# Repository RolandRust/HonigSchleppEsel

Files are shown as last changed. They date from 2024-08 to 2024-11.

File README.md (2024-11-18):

# HonigSchleppEsel
Turntable addon for the HaniMandl

## Kompiliert nur mit Visual Studio Code. Mit der Arduino IDE gibts Probleme!

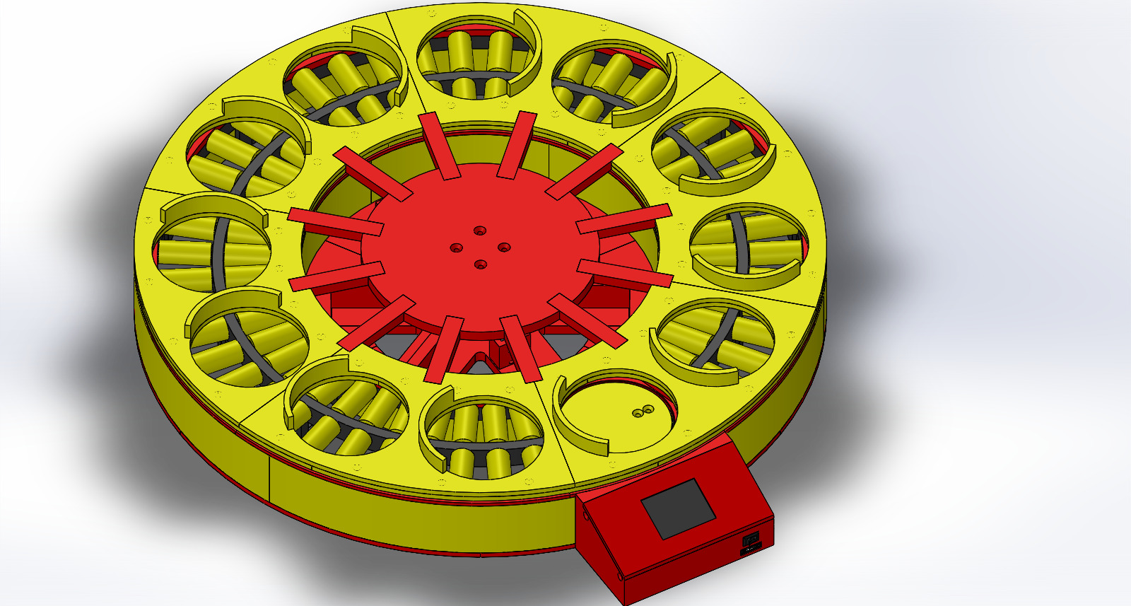
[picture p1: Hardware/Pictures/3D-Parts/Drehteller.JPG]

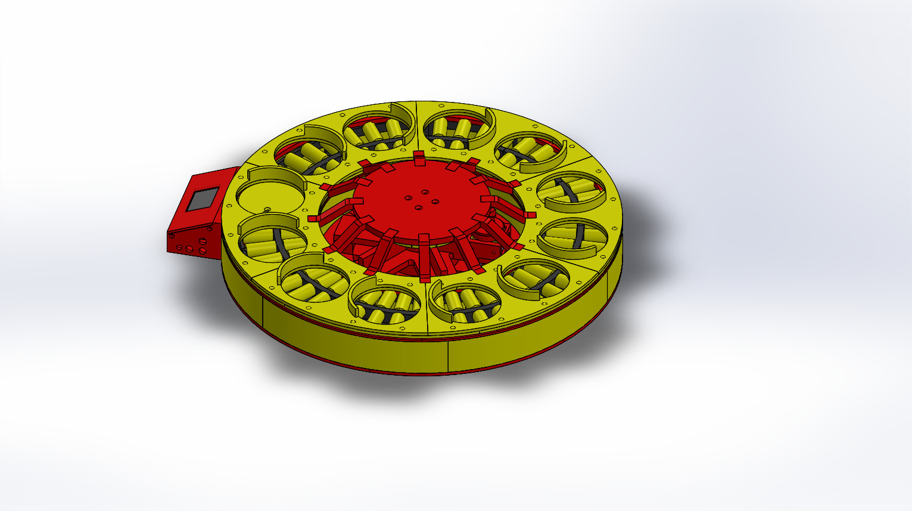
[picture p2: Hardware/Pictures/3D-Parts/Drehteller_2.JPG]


https://www.youtube.com/watch?v=Gq03sCifO4o

dev version

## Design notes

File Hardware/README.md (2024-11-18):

# Hardware
## Bottom middle assembly
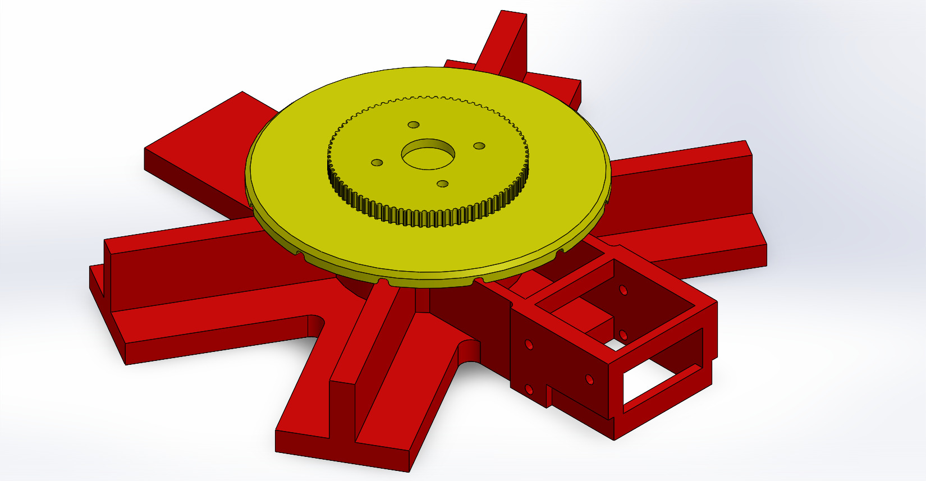
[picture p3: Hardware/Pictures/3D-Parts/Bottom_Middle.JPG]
bottom_middle

## Bottom middle optical switch assembly
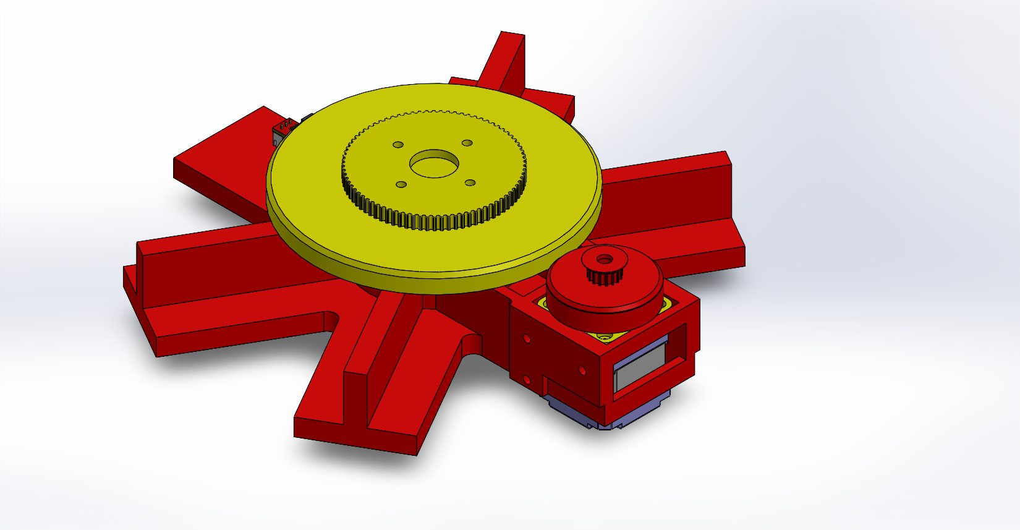
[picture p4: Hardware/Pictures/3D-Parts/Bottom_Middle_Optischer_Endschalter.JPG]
bottom_middle_optischer_endschalter

### Bottom_Middle
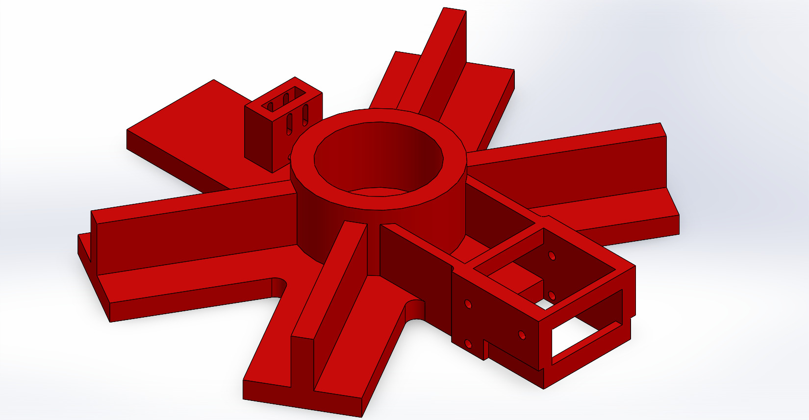
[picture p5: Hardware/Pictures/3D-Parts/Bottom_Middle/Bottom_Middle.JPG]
bottom_middle

### Bottom_Middle_Optischer_Schalter
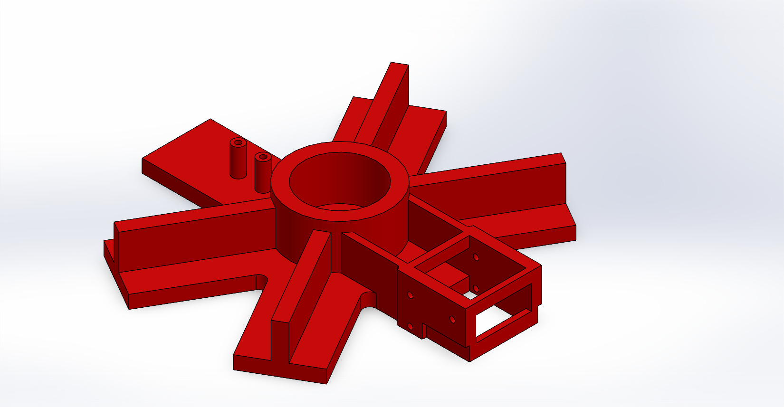
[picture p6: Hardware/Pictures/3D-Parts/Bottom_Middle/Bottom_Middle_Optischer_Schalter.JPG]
bottom_middle_optischer_schalter

### Mittelteil_Addon_30mm
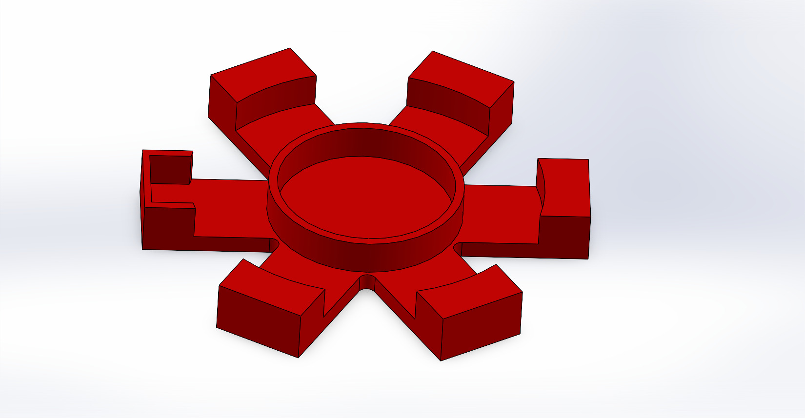
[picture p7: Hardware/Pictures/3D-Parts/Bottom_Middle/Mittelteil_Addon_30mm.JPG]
mittelteil_addon_30mm

### Umbau_zu_Optischem_Switch_Teil_1
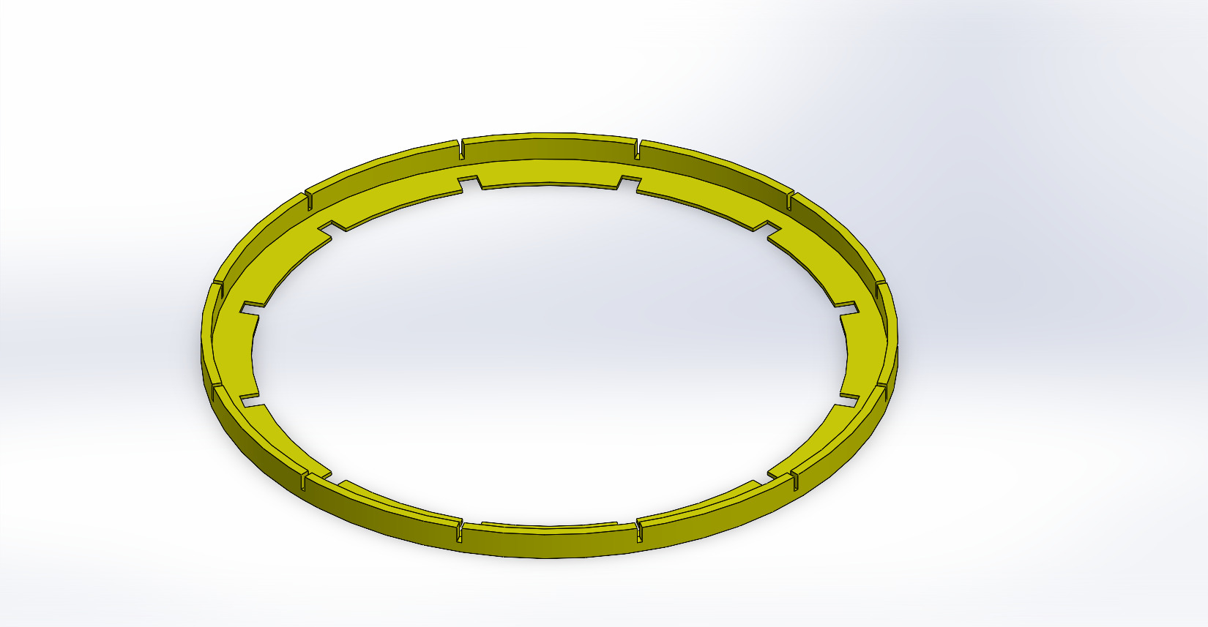
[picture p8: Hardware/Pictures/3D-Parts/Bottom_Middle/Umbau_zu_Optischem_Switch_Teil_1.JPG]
umbau_zu_optischem_switch_teil_1

### Umbau_zu_Optischem_Switch_Teil_2
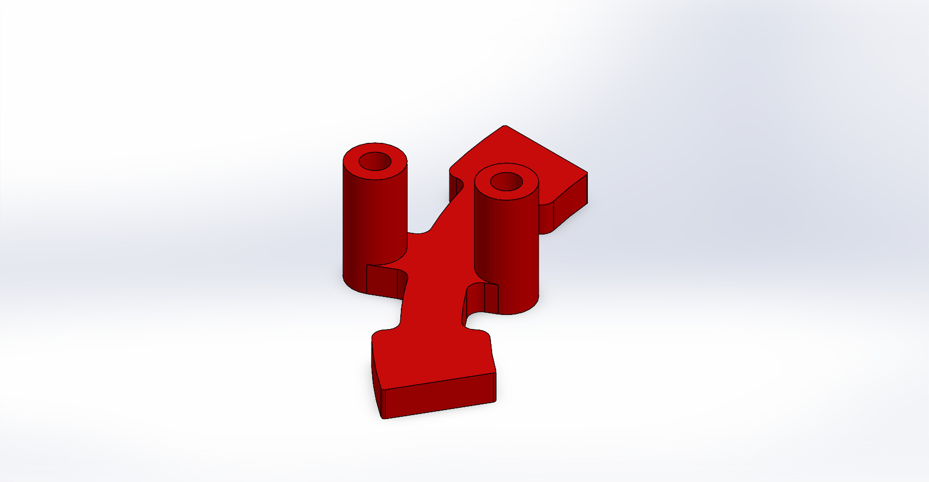
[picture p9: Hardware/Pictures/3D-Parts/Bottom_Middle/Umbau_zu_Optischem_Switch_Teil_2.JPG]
umbau_zu_optischem_switch_teil_2

### Umbau_zu_Optischem_Switch_Teil_3
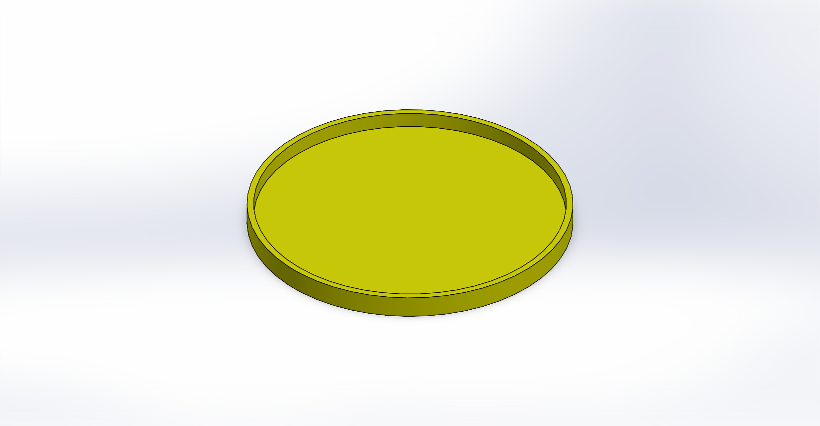
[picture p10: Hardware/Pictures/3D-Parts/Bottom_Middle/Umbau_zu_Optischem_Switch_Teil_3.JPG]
umbau_zu_optischem_switch_teil_3

### Mittelteil_Drehelement
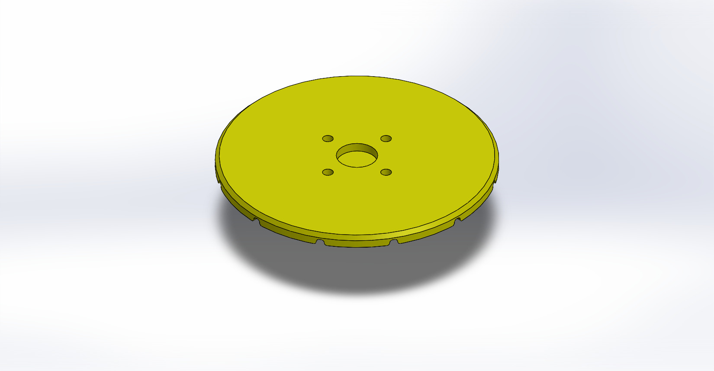
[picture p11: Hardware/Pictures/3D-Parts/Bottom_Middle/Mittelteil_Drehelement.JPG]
bottom_middle

### Mittelteil_Drehelement_Optischer_Endschalter
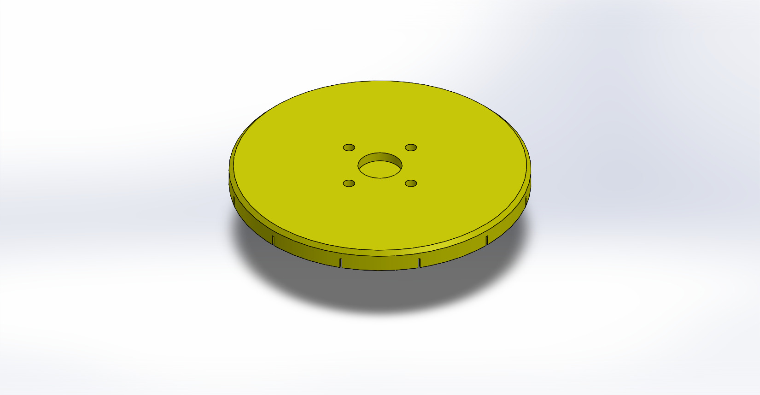
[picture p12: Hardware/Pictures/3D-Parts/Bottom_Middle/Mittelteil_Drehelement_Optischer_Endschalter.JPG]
bottom_middle

### HTD3_80_6.5
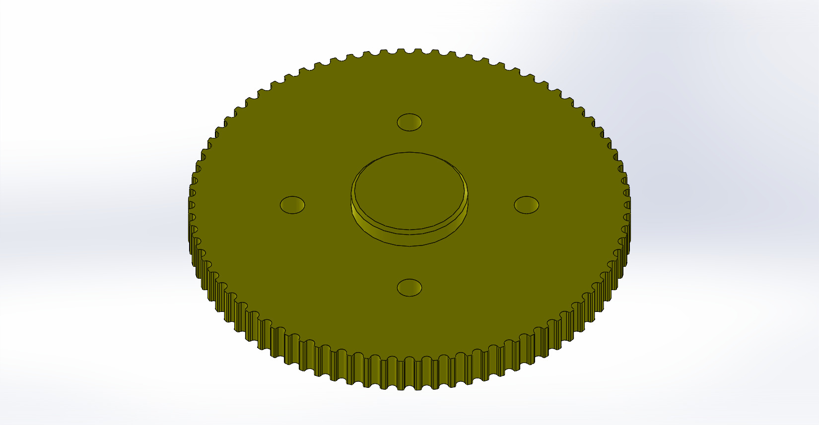
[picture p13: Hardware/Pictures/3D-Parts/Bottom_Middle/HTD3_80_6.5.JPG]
bottom_middle


## Bottom assembly
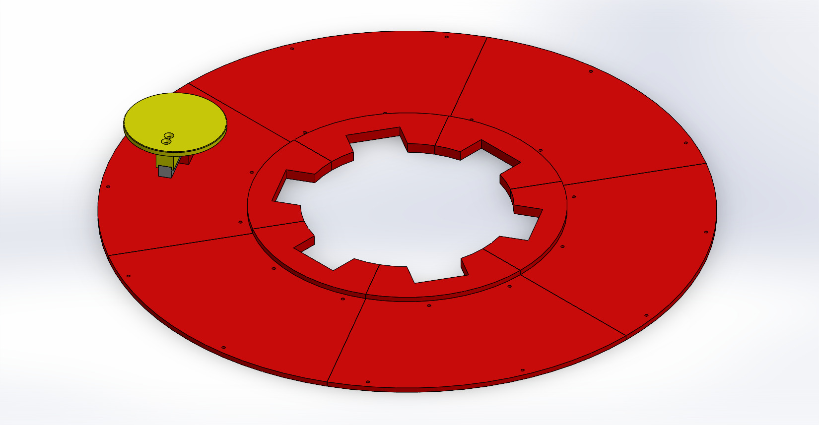
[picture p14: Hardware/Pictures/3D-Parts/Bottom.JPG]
bottom

### Bottom_Out
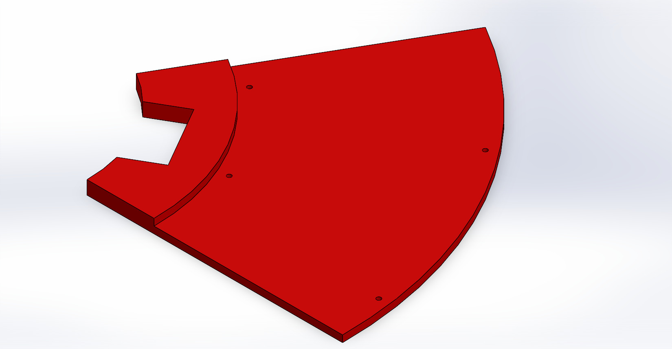
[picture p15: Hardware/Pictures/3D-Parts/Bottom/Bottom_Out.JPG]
bottom

### Bottom_Out_Scale
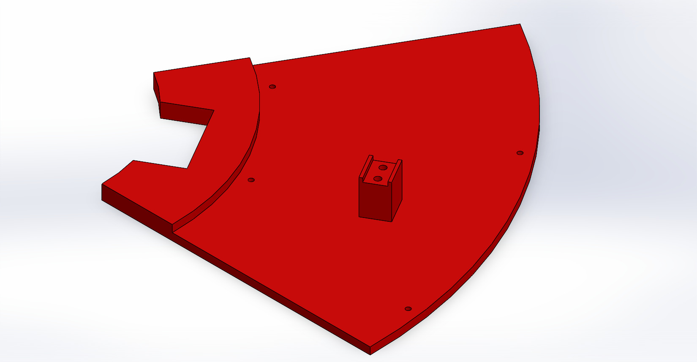
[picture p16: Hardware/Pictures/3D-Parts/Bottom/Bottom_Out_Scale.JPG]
bottom

### Scale_Top
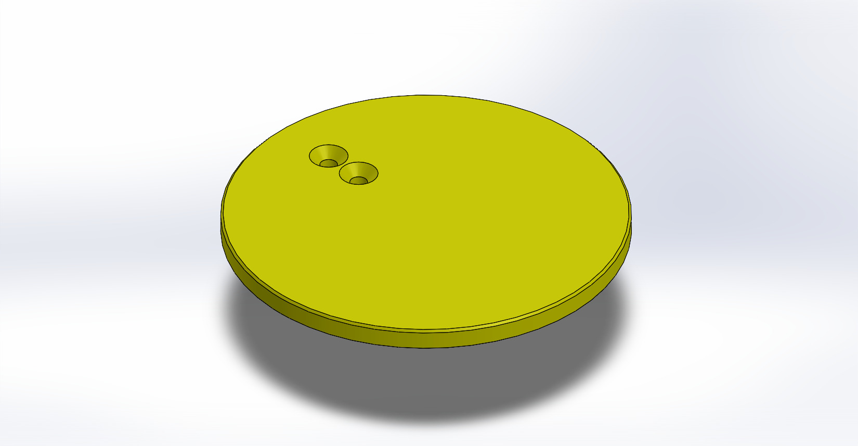
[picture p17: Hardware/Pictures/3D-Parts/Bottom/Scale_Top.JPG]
bottom


## 	Roll holder assembly
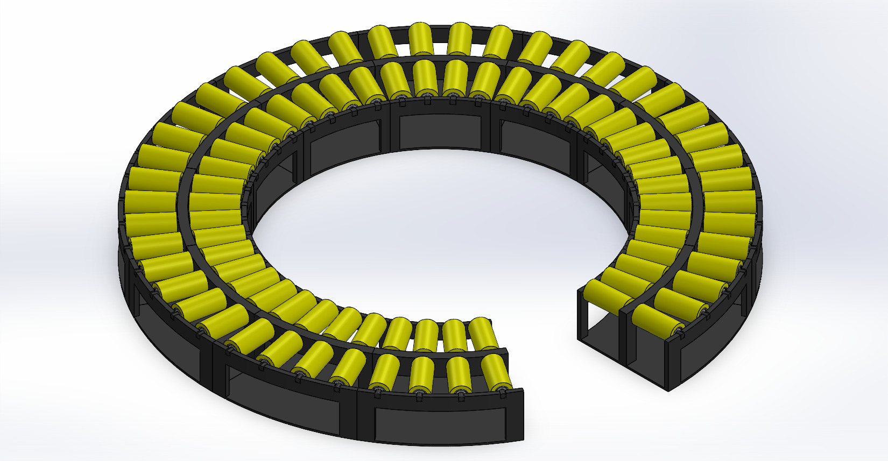
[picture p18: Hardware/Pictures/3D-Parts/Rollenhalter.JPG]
roll_holder

### Rollenhalter_klein
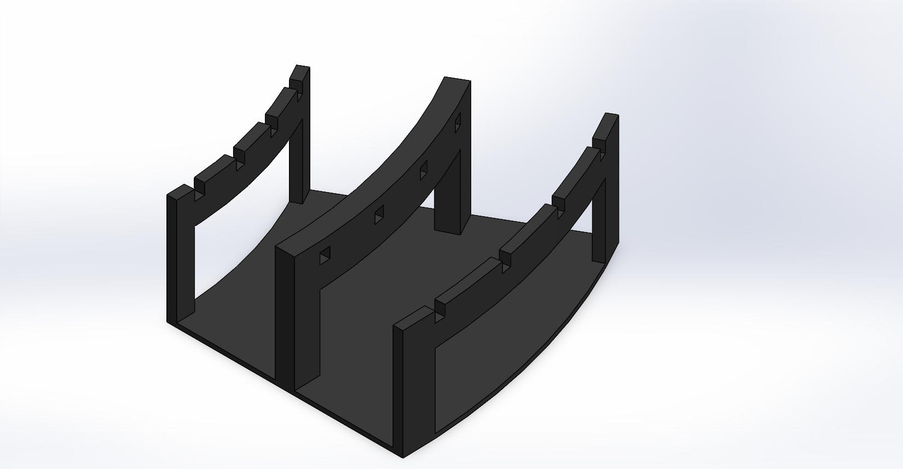
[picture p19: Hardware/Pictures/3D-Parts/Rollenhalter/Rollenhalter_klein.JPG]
roll_holder

### Rolle
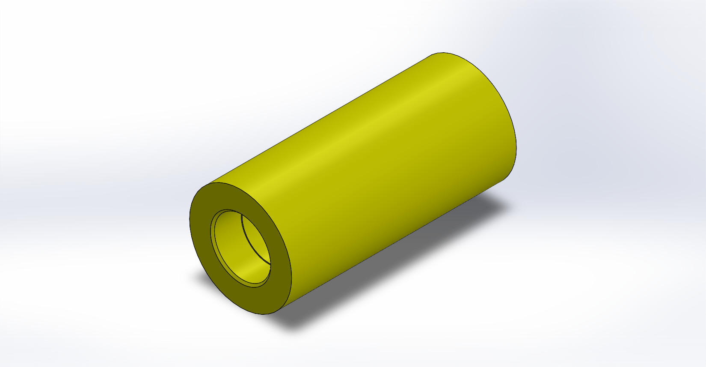
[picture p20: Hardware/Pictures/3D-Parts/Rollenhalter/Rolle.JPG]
roll_holder

### Zylinder_Stift
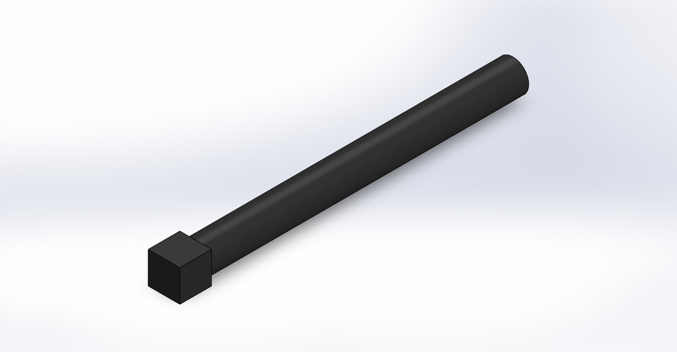
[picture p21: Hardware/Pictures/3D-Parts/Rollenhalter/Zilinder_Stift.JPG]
roll_holder


## 	Bottom top assembly
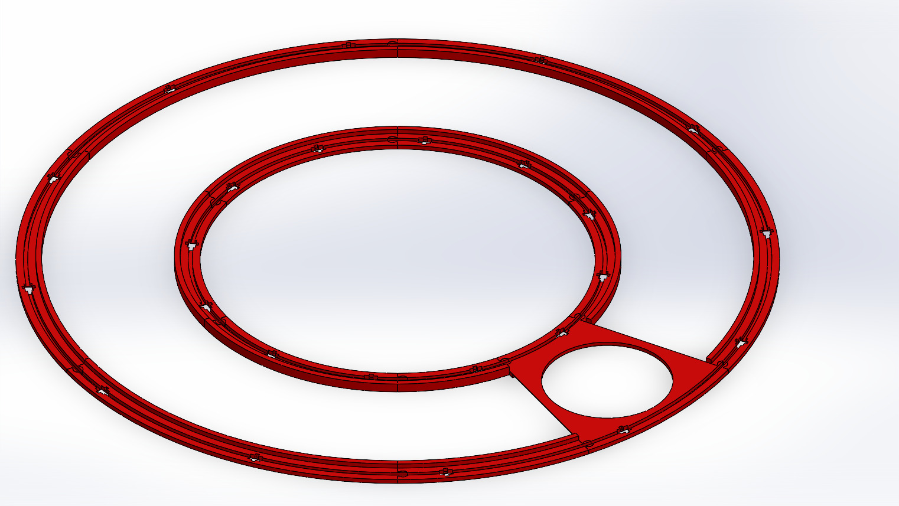
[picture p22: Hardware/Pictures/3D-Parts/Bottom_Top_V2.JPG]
bottom_top

### Top_Scale_V2
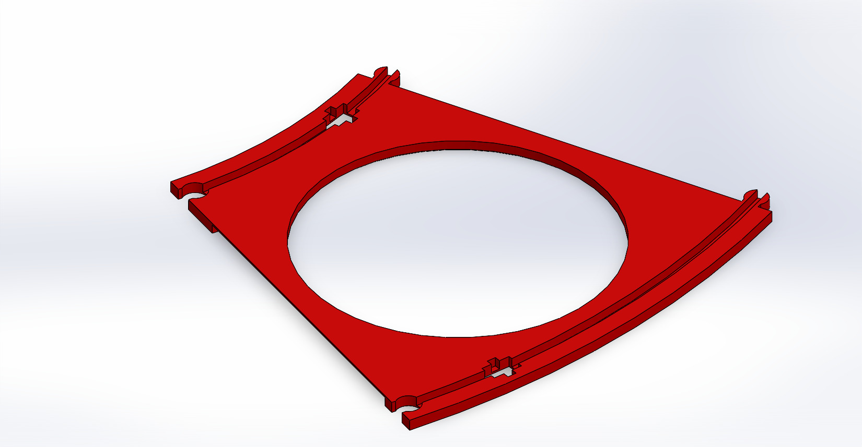
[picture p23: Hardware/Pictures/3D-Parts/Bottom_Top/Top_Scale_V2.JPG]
bottom_top

### Top_Ring_Big_Inside_V2
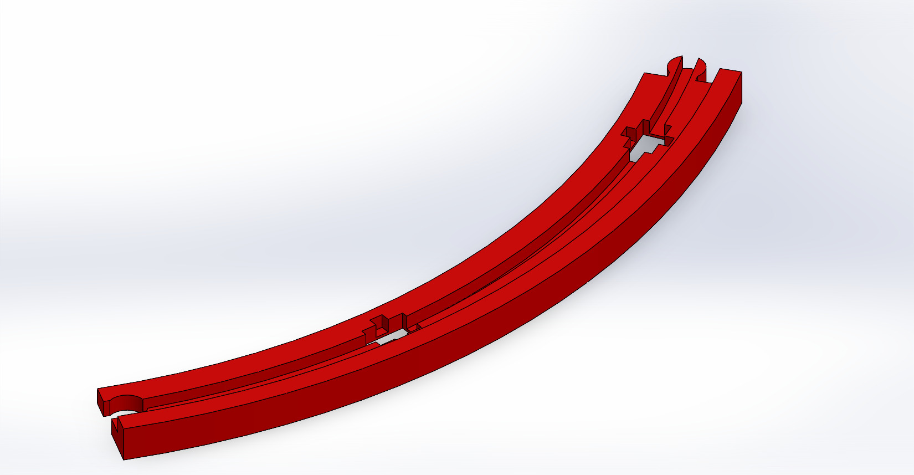
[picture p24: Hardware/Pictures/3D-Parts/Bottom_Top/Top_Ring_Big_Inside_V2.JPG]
bottom_top

### Top_Ring_Big_Outer_V2
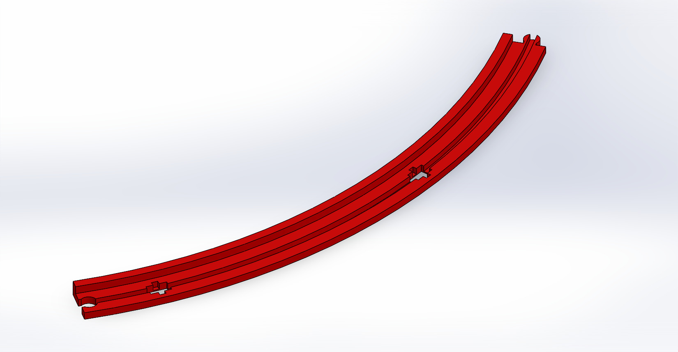
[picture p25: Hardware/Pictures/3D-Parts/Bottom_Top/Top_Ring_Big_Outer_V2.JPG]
bottom_top

### Top_Ring_Small_Inside_V2
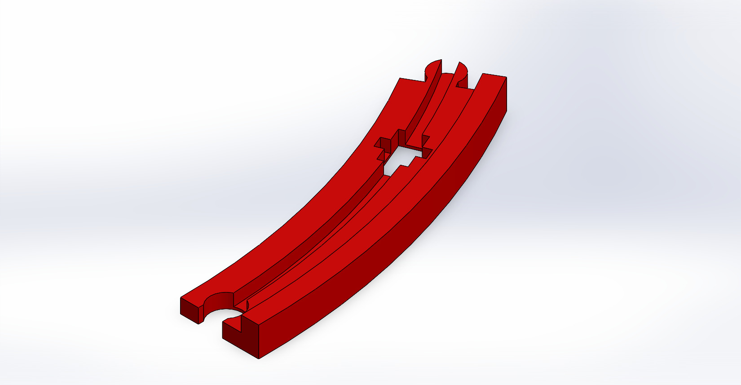
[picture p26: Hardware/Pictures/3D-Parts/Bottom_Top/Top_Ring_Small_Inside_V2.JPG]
bottom_top

### Top_Ring_Small_Outer_V2
bottom_top

## 	Wall inside assembly
wall_inside
### Wall_Inside_V2
wall_inside

## 	Wall outside assembly
wall_outside
### Wall_Inside_V2
wall_outside

## 	Top assembly
top
## 	Top_30mm assembly
top_30mm
### Top_Mittelteil_Drehelement
top
### Top_Jar_Mover_1
top
### Top_Jar_Mover_2
top
### Top_Holm
top
### Top_Holm_30mm
top_holm_30mm

## 	Front box
front_box
### Box_Bottom
front_box
### Box_Top
front_box

## 	Gear box
gear_box
### Carrier_Plate
gear_box
### Ring
gear_box
### Gear_Planet_0.5
gear_box
###Gear_Stepper_0.5
gear_box

## Fixes
### FIX_1
fixes
### FIX_2
fixes

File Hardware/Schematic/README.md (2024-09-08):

# Schematic
schematic

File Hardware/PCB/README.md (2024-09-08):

# PCB
PCB
PCB

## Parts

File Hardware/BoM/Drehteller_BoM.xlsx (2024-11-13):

Drehteller Stückliste (flache Version mit mechanischem Endschalter --> Motor schaut unter raus)
Version 1: | Flach mit mechanischem Taster für die Glaspositionierung (Stepper schaut unten raus)
Version 2: | Flach mit optischem Schalter für die Glaspositionierung (Stepper schaut unten raus)
Version 3: | Umbau der Version 1 auf optischen Schalter für die Glaspositionierung (Stepper schaut unten raus)
Version 4: | Umbau der Version 1 auf optischen Schalter für die Glaspositionierung und Erhöhung von dem Mittelteil (Stepper schaut unten nicht raus)
Version 5: | Optischer Endschalter für die Glaspositionierung und Erhöhung vom Mittelteil --> empfohlene Version
Remarks: | Wenn mein Pseudo Getriebe aufgiebt, werde ich es durch ein gekaugtes ersetzen. Für ein gekauftes Getriebe muss noch eine Befestigung ausgedacht werden.
 | Version 1 | Version 2 | Version 3 | Version 4 | Version 5
Bottom_Middle
POS | Anzahl | Anzahl | Anzahl | Anzahl | Anzahl | Beschreibung
1 | 1 | - | 1 | 1 | - | Bottom_Middle | 3D Druck
2 | - | 1 | - | - | 1 | Bottom_Middle_Optischer_Schalter | 3D Druck
3 | - | - | - | 1 | 1 | Mittelteil_Addon_30mm | 3D Druck
4 | - | - | - | - | - | Bottom_Middle_30mm (noch nicht gezeichnet) | 3D Druck | ersetzt Bottom_Middle_Optischer_Schalter und Mittelteil_Addon_30mm vei der Variante 5
5 | 1 | - | 1 | 1 | - | Mittelteil_Drehelement | 3D Druck
6 | - | 1 | - | - | 1 | Mittelteil_Drehelement_Optischer_Endschalter (noch nicht gezeichnet) | 3D Druck | noch nicht fertig gezeichnet
7 | 1 | 1 | 1 | 1 | 1 | HTD3_80_6.5 | 3D Druck
8 | - | - | - | 1 | - | Umbau_zu_Optischem_Switch_Teil_1 | 3D Druck | mit schwarzem PET drucken. Durch gelbes PETG konnte bei mir der optische Schalter durchsehen.
9 | - | - | - | 1 | - | Umbau_zu_Optischem_Switch_Teil_2 | 3D Druck
10 | - | - | - | 1 | - | Umbau_zu_Optischem_Switch_Teil_3 | 3D Druck
11 | 1 | - | 1 | - | - | Mikro Schalter Endschalter mit Momentanem Roller Hebel Arm SPDT | gekauft
12 | - | 1 | - | 1 | 1 | TCST2103 Optische Endstop Light Control Begrenzung Optische Schalter für 3D Drucker | gekauft
13 | 1 | 1 | 1 | 1 | 1 | Axial-Nadelkranz AXK3047 mit 2 Unterlagssccheiben | gekauft
14 | 1 | 1 | 1 | 1 | 1 | Nadellager Radial 50*55*27mm K505527 | gekauft
15 | 2 | 2 | 2 | 2 | 2 | Schraube, Mutter und Unterlagsscheibe für Mikro Endschalter | gekauft
16 | 4 | 4 | 4 | 4 | 4 | Gewindeeinsätze für 3D Druck M4xL8xOD6 | gekauft
17 | 1 | 1 | 1 | 1 | 1 | HTD 3M Zahnriemen 6mm x 351mm | gekauft
Top
POS | Anzahl | Anzahl | Anzahl | Anzahl | Anzahl | Beschreibung
1 | 6 | 6 | 6 | 6 | 6 | Top_Jar_Mover_1 | 3D Druck
2 | 6 | 6 | 6 | 6 | 6 | Top_Jar_Mover_2 | 3D Druck
3 | 12 | 12 | 12 | - | - | Top_Holm | 3D Druck
4 | - | - | - | 12 | 12 | Top_Holm_30mm | 3D Druck
5 | 1 | 1 | 1 | 1 | 1 | Top_Mittelteil_Drehelement | 3D Druck
5 | 4 | 4 | 4 | 4 | 4 | Schrauben | gekauft
Rollenhalter
POS | Anzahl | Anzahl | Anzahl | Anzahl | Anzahl | Beschreibung
1 | 11 | 11 | 11 | 11 | 11 | Rollenhalter_klein | 3D Druck
2 | 88 | 88 | 88 | 88 | 88 | Rolle | 3D Druck
3 | 88 | 88 | 88 | 88 | 88 | Zilinder_Stift | 3D Druck
4 | 176 | 176 | 176 | 176 | 176 | Rillenkugellager 685zz | gekauft
Bottom_Top
POS | Anzahl | Anzahl | Anzahl | Anzahl | Anzahl | Beschreibung
1 | 1 | 1 | 1 | 1 | 1 | Top_Scale_V2 | 3D Druck
2 | 5 | 5 | 5 | 5 | 5 | Top_Ring_Big_Inside_V2 | 3D Druck
3 | 1 | 1 | 1 | 1 | 1 | Top_Ring_Smal_Inside_V2 | 3D Druck
4 | 5 | 5 | 5 | 5 | 5 | Top_Ring_Big_Outer_V2 | 3D Druck
5 | 1 | 1 | 1 | 1 | 1 | Top_Ring_Small_Inside_V2 | 3D Druck
Wall_Inside
POS | Anzahl | Anzahl | Anzahl | Anzahl | Anzahl | Beschreibung
1 | 6 | 6 | 6 | 6 | 6 | Wall_Inside_V2 | 3D Druck
2 | 12 | 12 | 12 | 12 | 12 | Rillenkugellager 693zz | gekauft
3 | 12 | 12 | 12 | 12 | 12 | Zylinderstift M3x10mm | gekauft
4 | 12 | 12 | 12 | 12 | 12 | Gewindeeinsätze für 3D Druck M3xL8xOD5 | gekauft
5 | 12 | 12 | 12 | 12 | 12 | Schrauben zur Besestigung an die Baugruppe Bottom | gekauft
Wall_Outside
POS | Anzahl | Anzahl | Anzahl | Anzahl | Anzahl | Beschreibung
1 | 6 | 6 | 6 | 6 | 6 | Wall_Outside_V2 | 3D Druck
2 | 12 | 12 | 12 | 12 | 12 | Rillenkugellager 693zz | gekauft
3 | 12 | 12 | 12 | 12 | 12 | Zylinderstift M3x10mm | gekauft
4 | 12 | 12 | 12 | 12 | 12 | Gewindeeinsätze für 3D Druck M3xL8xOD5 | gekauft
5 | 12 | 12 | 12 | 12 | 12 | Schrauben zur Besestigung an die Baugruppe Bottom | gekauft
Bottom
POS | Anzahl | Anzahl | Anzahl | Anzahl | Anzahl | Beschreibung
1 | 1 | 1 | 1 | 1 | 1 | Bottom_Out_Scale | 3D Druck
2 | 5 | 5 | 5 | 5 | 5 | Bottom_Out | 3D Druck
3 | 1 | 1 | 1 | 1 | 1 | Scale_Top | 3D Druck
4 | 1 | 1 | 1 | 1 | 1 | Wägezelle 5kg | gekauft
5 | 4 | 4 | 4 | 4 | 4 | Schrauben für die Waage | gekauft
Front
POS | Anzahl | Anzahl | Anzahl | Anzahl | Anzahl | Beschreibung
1 | 1 | 1 | 1 | 1 | 1 | Box_Bottom | 3D Druck
2 | 1 | 1 | 1 | 1 | 1 | Box_Top | 3D Druck
3 | 4 | 4 | 4 | 4 | 4 | Gewindeeinsätze für 3D Druck M3xL8xOD5 | gekauft
4 | 4 | 4 | 4 | 4 | 4 | Schrauben zur befestigung des Deckels | gekauft
Pseudo Planeten Getriebe
POS | Anzahl | Anzahl | Anzahl | Anzahl | Anzahl | Beschreibung
1 | 1 | 1 | 1 | 1 | 1 | Carrier_Plate | 3D Druck
2 | 1 | 1 | 1 | 1 | 1 | Ring | 3D Druck
3 | 4 | 4 | 4 | 4 | 4 | Gear_Planet_0.5 | 3D Druck
4 | 1 | 1 | 1 | 1 | 1 | Gear_Stepper_0.5 | 3D Druck
5 | 4 | 4 | 4 | 4 | 4 | Schrauben zur Besestigung der Gearbox am Stepper | gekauft
6 | 1 | 1 | 1 | 1 | 1 | NEMA17 Stepper Motor h: 40mm | gekauft
7 | 4 | 4 | 4 | 4 | 4 | Schrauben zur Besestigung von dem NEMA17 an der Baugruppe Bottom_Middle | gekauft
Fixes (ja die braucht es :-))
POS | Anzahl | Anzahl | Anzahl | Anzahl | Anzahl | Beschreibung
1 | 3 | 3 | 3 | 3 | 3 | FIX_1 | 3D Druck
2 | 1 | 1 | 1 | 1 | 1 | FIX_2 | 3D Druck
Diverser
POS | Anzahl | Anzahl | Anzahl | Anzahl | Anzahl | Beschreibung
1 | 1 | 1 | 1 | 1 | 1 | Leim nach Wahl | gekauft

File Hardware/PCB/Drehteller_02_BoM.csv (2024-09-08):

# | Quantity | RefDes | Manufacturer | Order Number | Description
1 | 1 | C1 | RND components | RND 150VVT050M101FB3 | Miniature Aluminium Electrolytic Capacitor 100uF 50V ±20% 8x10.5mm
2 | 1 | D1 | Nexperia | PMEG4030EP | 40 V, 3 A low VF Schottky barrier rectifier
3 | 5 | J1, J3, J5, J11, J12 | Diverse | - | JST XH 2pol Connector 2.54mm (not orginal JST standart)
4 | 7 | J2, J6, J7, J8, J9, J15, J17 | Diverse | - | JST XH 4pol Connector 2.54mm (not orginal JST standart)
5 | 3 | J4, J18, J19 | Diverse | - | JST XH 3pol Connector 2.54mm (not orginal JST standart)
6 | 1 | J10 | Samtec | TSW-104-07-G-S | 1x4 Pol Connector 100mil
7 | 1 | J16 | Diverse | - | JST XH 7pol Connector 2.54mm (not orginal JST standart)
8 | 1 | M1 | Diverse | - | ESP32 NodeMCU Module WLAN WiFi Development Board Socket
9 | 1 | M2 | Diverse | - | MP1584 Module Socket
10 | 1 | M3 | Diverse | - | TMC2209 Silent Stepper Stick Socket
11 | 4 | R1, R2, R3, R4 | Vishay | MCT06030Z0000ZP500 | Resistor 0R 1% 0603

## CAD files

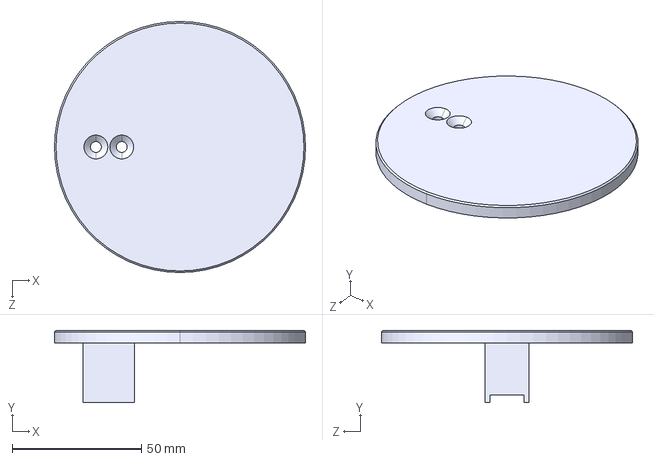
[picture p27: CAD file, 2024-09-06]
Hardware/STEP-Files/Bottom/Scale_Top.STEP
97.0 x 28.0 x 97.0 mm

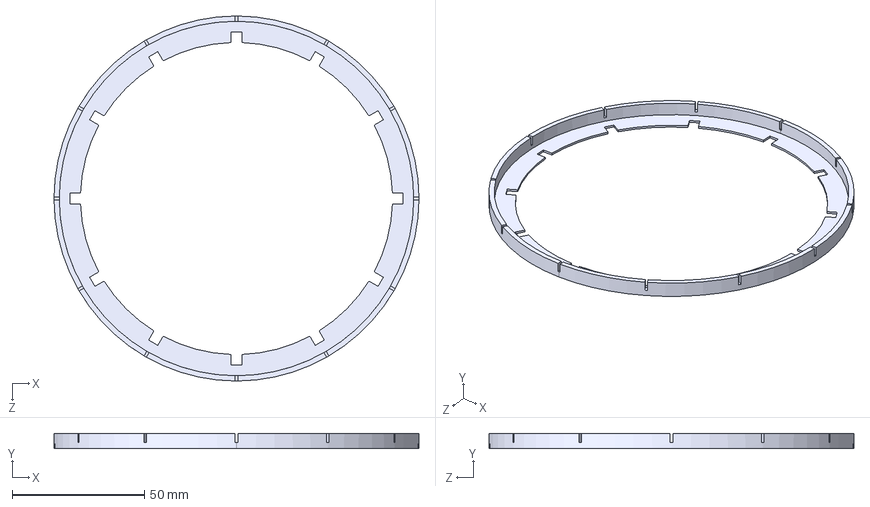
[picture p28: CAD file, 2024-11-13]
Hardware/STEP-Files/Bottom_Middle/Umbau_zu_Optischem_Switch_Teil_1.STEP
138.0 x 5.80 x 138.0 mm

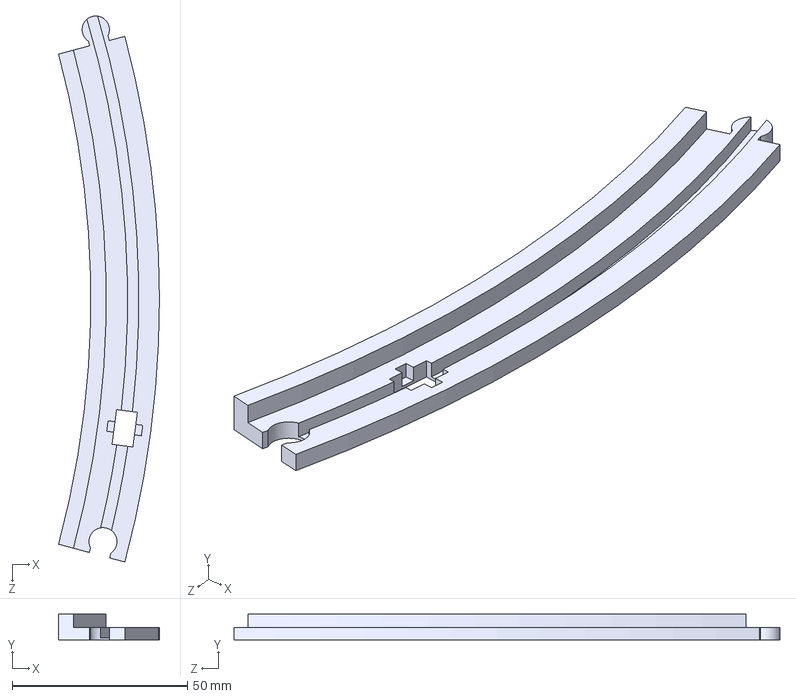
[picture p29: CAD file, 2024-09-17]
Hardware/STEP-Files/Bottom_Top/Top_Ring_Small_Outer_V2.STEP
28.8 x 7.40 x 155.9 mm

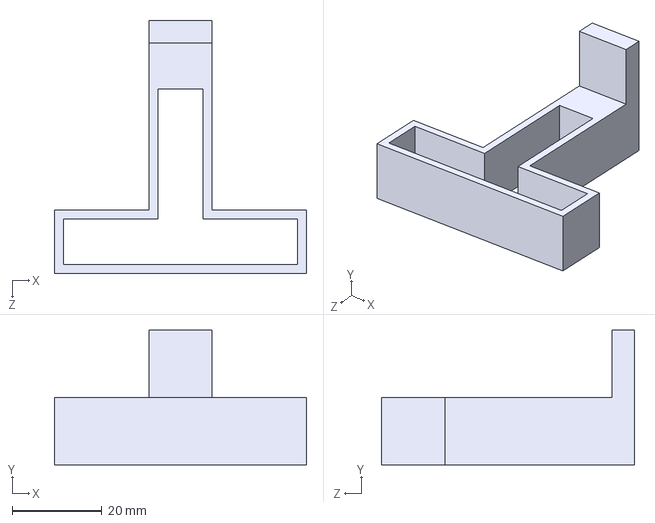
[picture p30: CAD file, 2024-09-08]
Hardware/STEP-Files/Fixes/FIX_1.STEP
56.1 x 30.0 x 56.3 mm

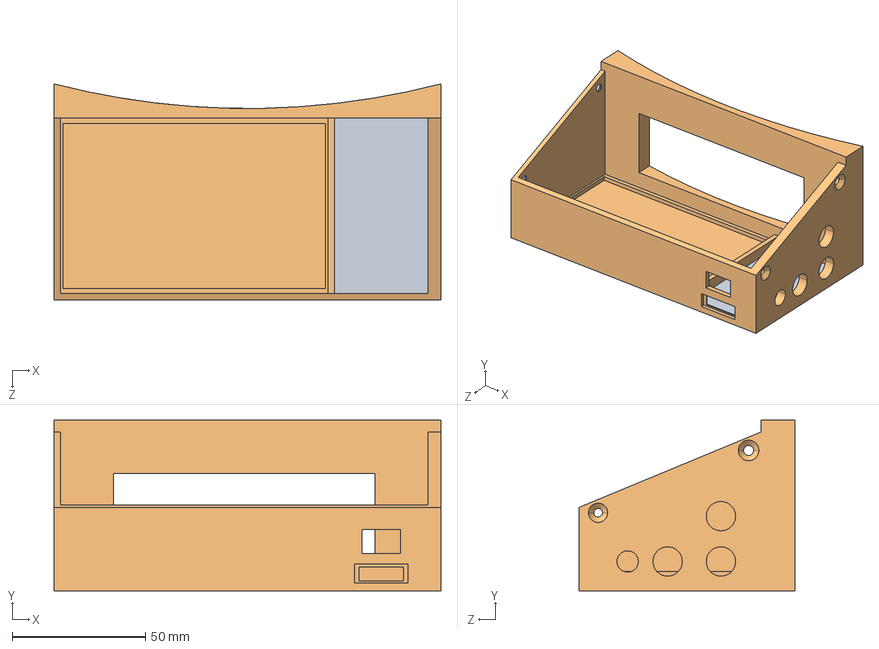
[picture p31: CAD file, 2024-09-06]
Hardware/STEP-Files/Front_Box/Box_Bottom.STEP
145.2 x 64.0 x 81.1 mm

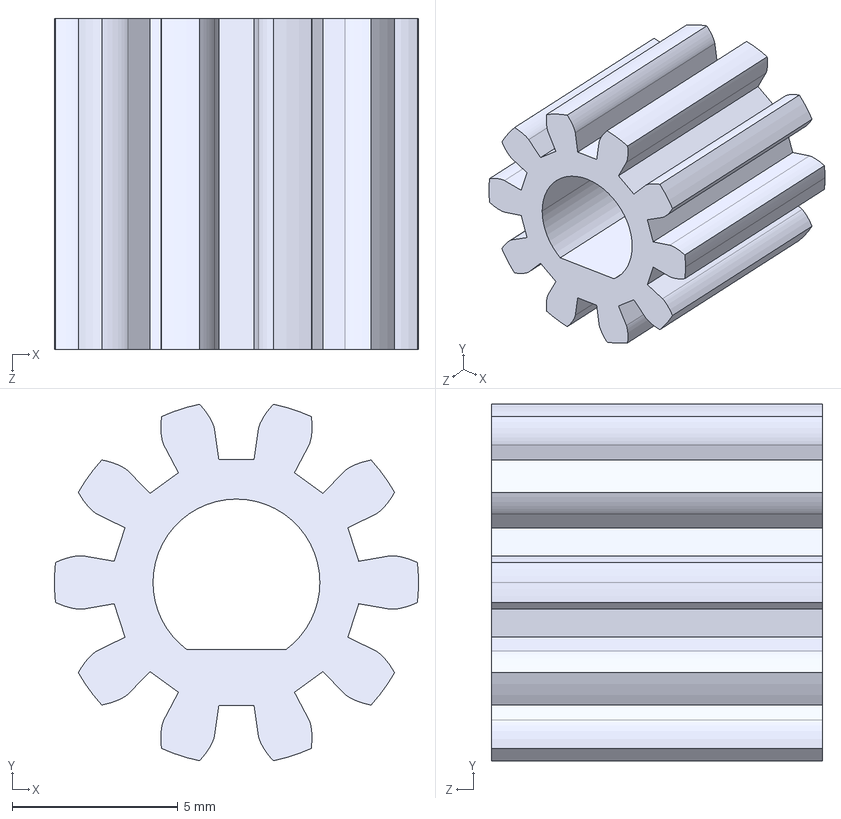
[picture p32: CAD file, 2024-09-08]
Hardware/STEP-Files/GearBox/Gear_Stepper_0.5.STEP
11.0 x 10.8 x 10.0 mm

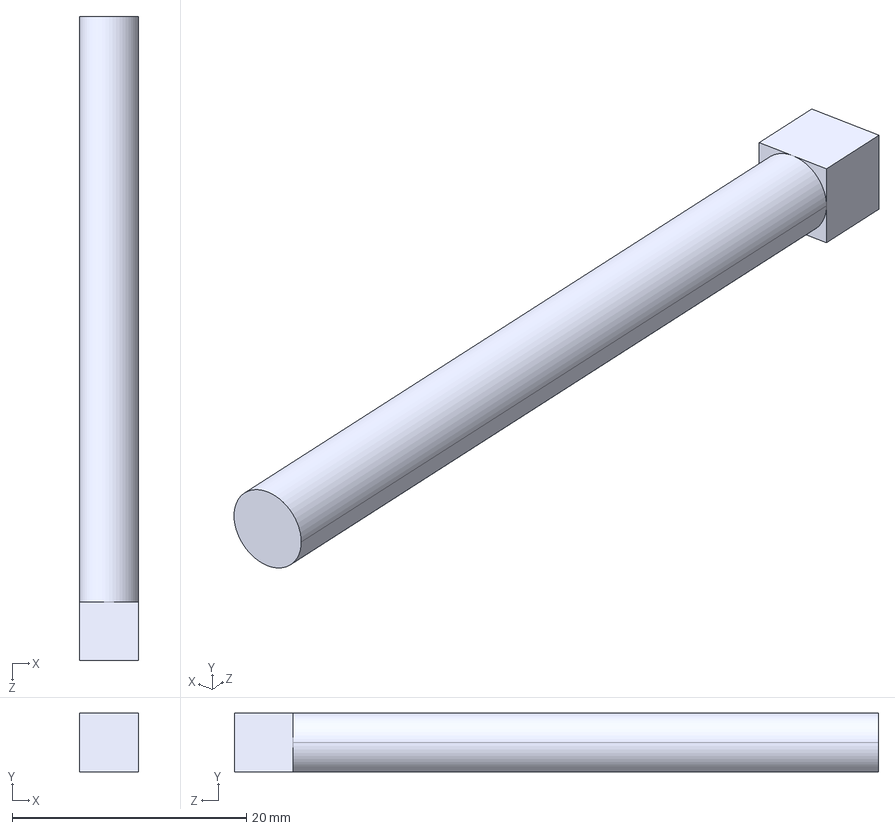
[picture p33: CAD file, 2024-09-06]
Hardware/STEP-Files/Rollenhalter/Zilinder_Stift.STEP
5.00 x 5.00 x 55.0 mm

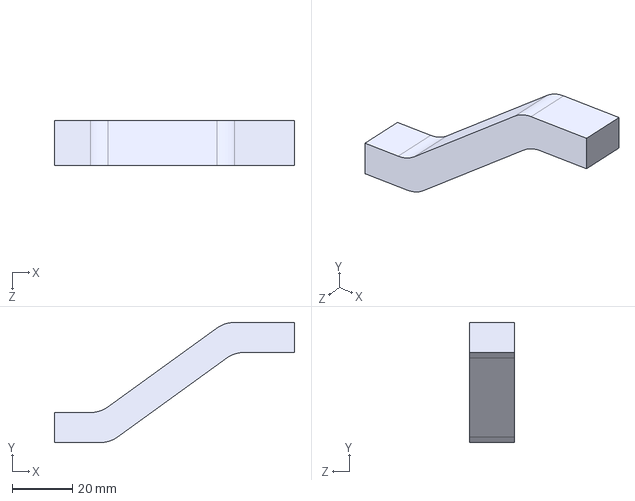
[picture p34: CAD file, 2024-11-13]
Hardware/STEP-Files/Top/Top_Holm_30mm.STEP
79.9 x 40.0 x 15.0 mm

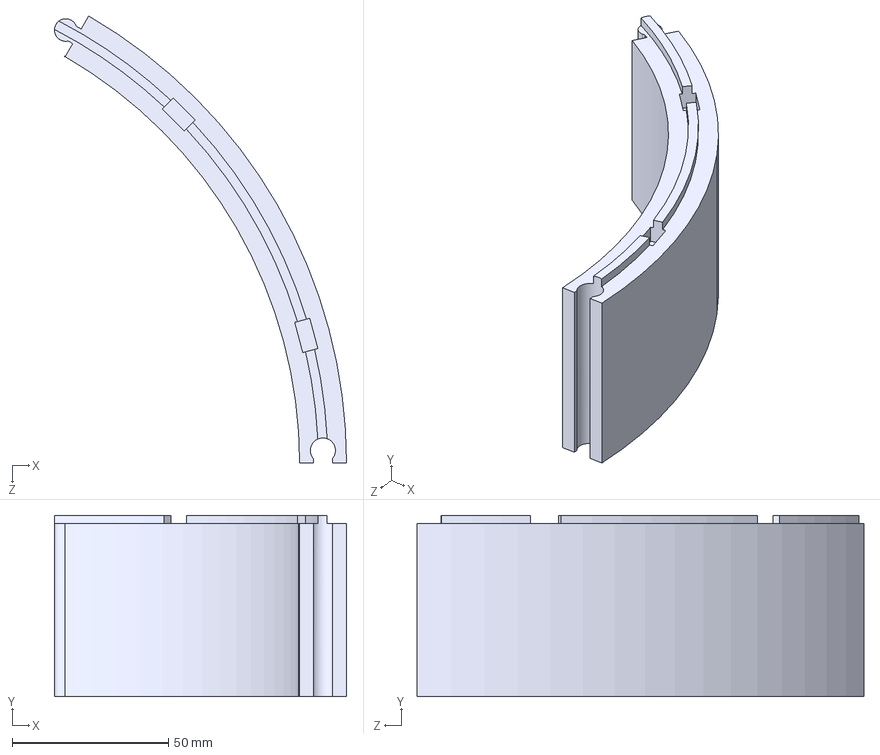
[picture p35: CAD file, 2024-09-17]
Hardware/STEP-Files/Wall_Inside/Wall_Inside_V2.STEP
93.3 x 58.0 x 142.8 mm

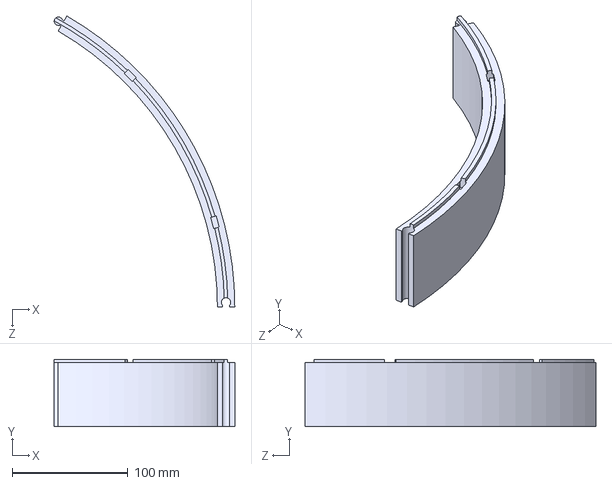
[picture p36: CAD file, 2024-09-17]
Hardware/STEP-Files/Wall_Outside/Wall_Outside_V2.STEP
155.8 x 58.0 x 251.1 mm

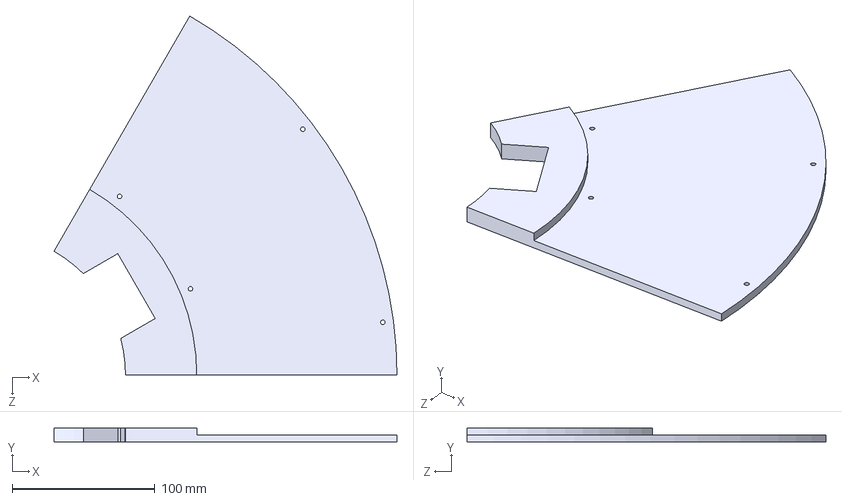
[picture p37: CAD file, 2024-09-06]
Hardware/STEP-Files/Bottom/Bottom_Out.STEP
240.0 x 10.0 x 251.1 mm

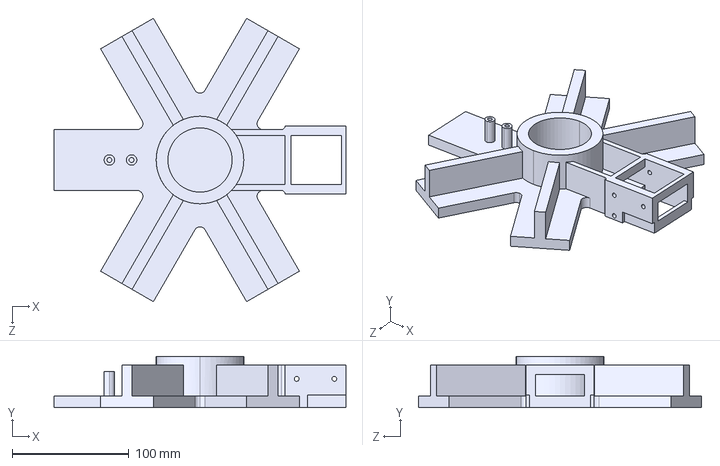
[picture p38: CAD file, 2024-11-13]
Hardware/STEP-Files/Bottom_Middle/Bottom_Middle_Optischer_Endschalter.STEP
250.0 x 44.0 x 242.6 mm

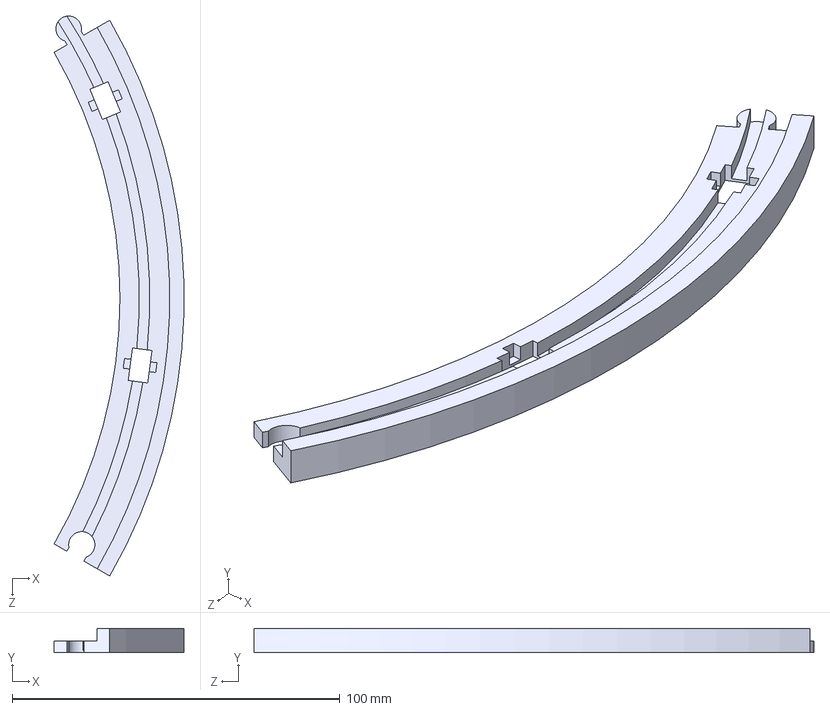
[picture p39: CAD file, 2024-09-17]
Hardware/STEP-Files/Bottom_Top/Top_Ring_Big_Inside_V2.STEP
39.6 x 7.40 x 170.9 mm

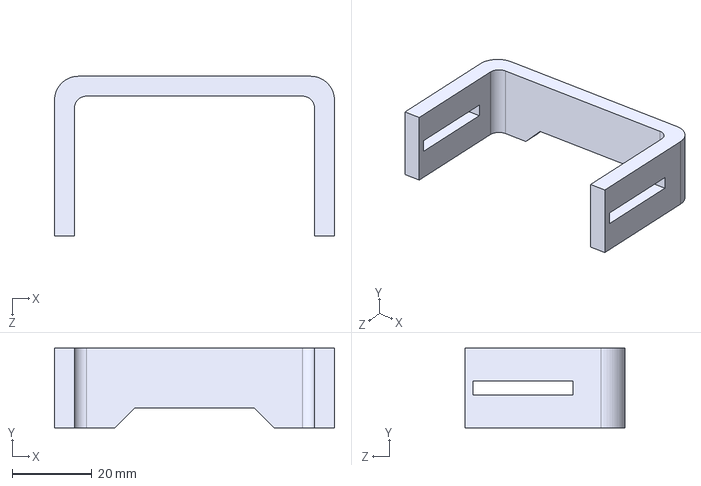
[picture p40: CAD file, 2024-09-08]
Hardware/STEP-Files/Fixes/FIX_2.STEP
70.2 x 20.0 x 40.0 mm

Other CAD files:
Hardware/STEP-Files/Front_Box/Box_Top.STEP
Hardware/STEP-Files/GearBox/Ring.STEP
Hardware/STEP-Files/Rollenhalter/Rollenhalter_klein.STEP
Hardware/STEP-Files/Top/Top_Jar_Mover_1.STEP
Hardware/STEP-Files/Bottom/Bottom_Out_Scale.STEP
Hardware/STEP-Files/Bottom_Middle/Bottom_Middle.STEP
Hardware/STEP-Files/Bottom_Middle/HTD3_80_6.5.STEP
Hardware/STEP-Files/Bottom_Middle/Mittelteil_Addon_30mm.STEP
Hardware/STEP-Files/Bottom_Middle/Mittelteil_Drehelement.STEP
Hardware/STEP-Files/Bottom_Middle/Umbau_zu_Optischem_Switch_Teil_2.STEP
Hardware/STEP-Files/Bottom_Top/Top_Ring_Big_Outer_V2.STEP
Hardware/STEP-Files/Bottom_Top/Top_Ring_Small_Inside_V2.STEP
Hardware/STEP-Files/Bottom_Top/Top_Scale_V2.STEP
Hardware/STEP-Files/GearBox/Carrier_Plate.STEP
Hardware/STEP-Files/GearBox/Gear_Planet_0.5.STEP
Hardware/STEP-Files/Rollenhalter/Rolle.STEP
Hardware/STEP-Files/Top/Top_Holm.STEP
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

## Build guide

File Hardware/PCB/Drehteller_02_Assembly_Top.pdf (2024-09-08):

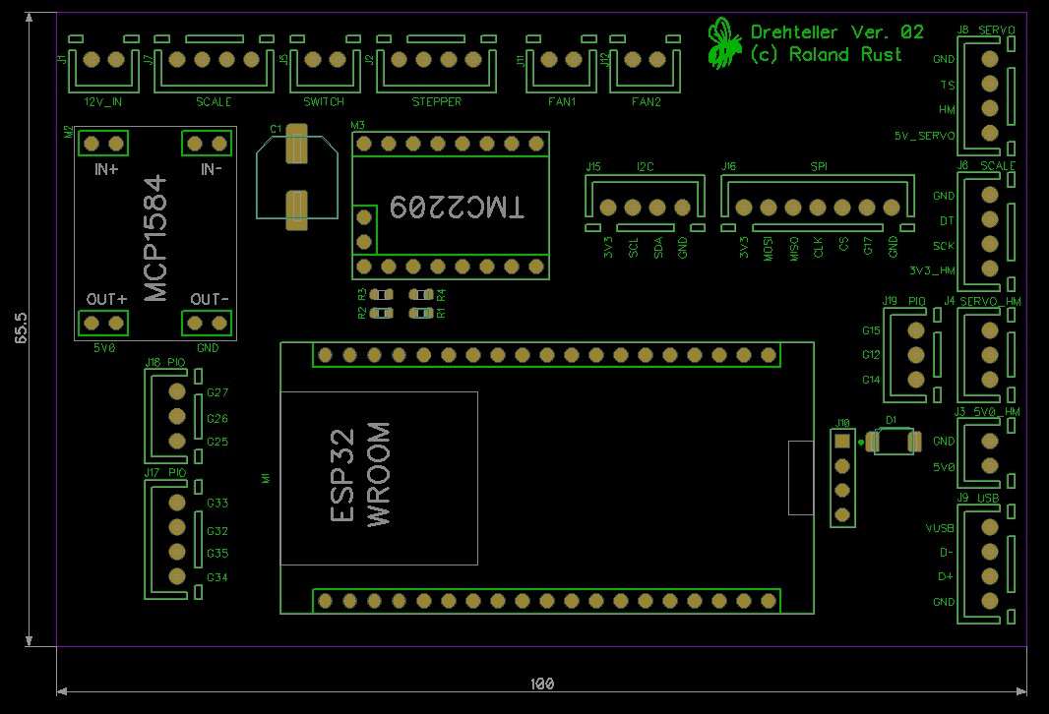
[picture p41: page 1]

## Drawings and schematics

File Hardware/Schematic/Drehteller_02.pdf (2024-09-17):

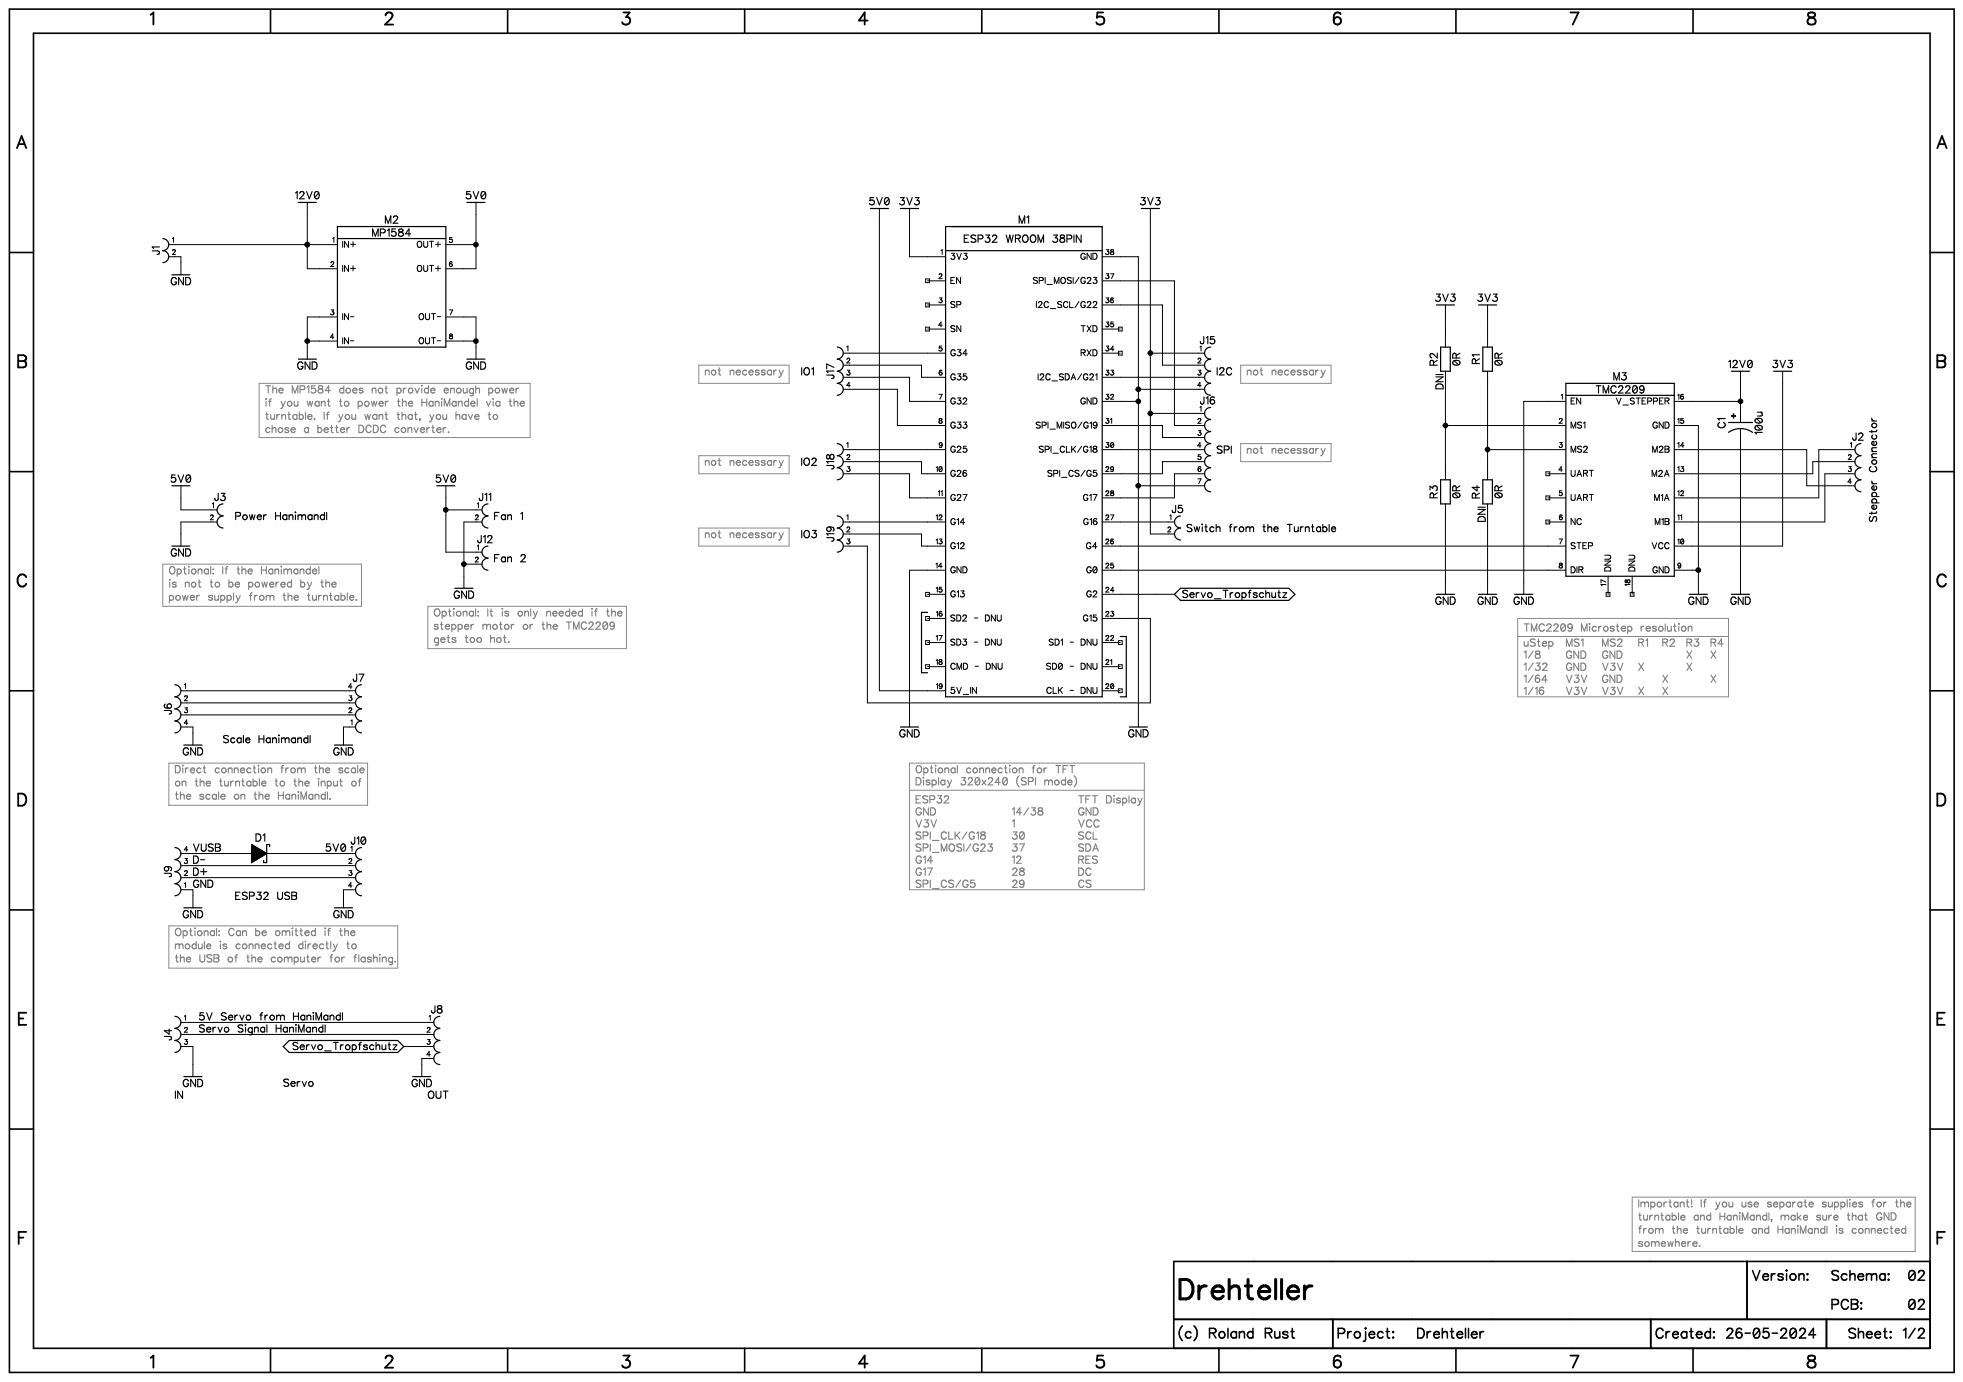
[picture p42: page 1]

the scale on the HaniMandl.

Optional connection for TFT
Display 320x240 (SPI mode)

Important! If you use separate supplies for the
turntable and HaniMandl, make sure that GND
from the turntable and HaniMandl is connected
somewhere.

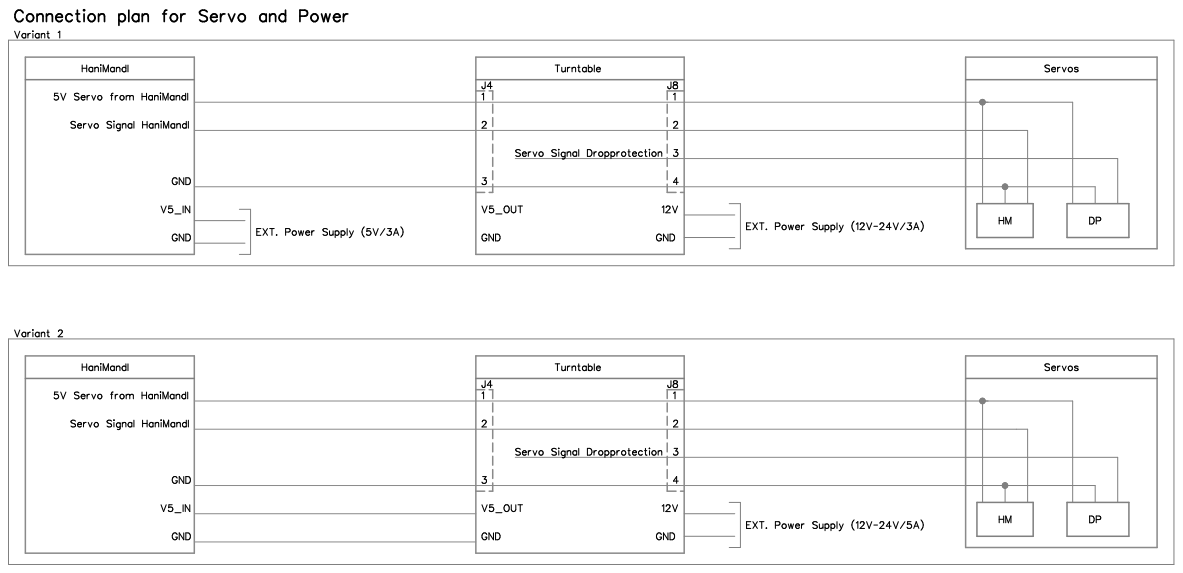
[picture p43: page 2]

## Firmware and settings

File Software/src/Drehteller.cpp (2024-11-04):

#include <Arduino.h>
#include <esp_now.h>
#include <WiFi.h>
#include <esp_wifi.h>
#include <Preferences.h>
#include <ESP32Servo.h>
#include <SPI.h>

String version = "0.0.1";

//#define DEBUG
//#define DEBUG_INI
#define READ_PREFERENCES
#define USE_DISPLAY 1               // 0 = no display conected, 1 = display conected
#define USE_INIT_CORR 1             // 0 = no init correctur, 1 = init correctur (can be usefull if the gear is 3D ptinted)
#define CHANGE_MAC_ADDRESS_HM 1     // HaniMandl: 0 = do not change the mac address, 1 = change the mac address
#define CHANGE_MAC_ADDRESS_TT 1     // Turntable: 0 = do not change the mac address, 1 = change the mac address
#define OTA_UPDATE 1                // 0: OTA update disabled, 1: OTA update enabled
#define SWITCH_TYPE 1               // 0: Mechanical switch, 1: Optical switch

Preferences preferences;

//ESP Now
#if CHANGE_MAC_ADDRESS_HM == 0
  #include "./Resources/mac.h"
#endif
#if CHANGE_MAC_ADDRESS_HM == 1
  const uint8_t MacAdressHanimandl[] = {0x74, 0x00, 0x00, 0x00, 0x00, 0x01};
#endif
esp_now_peer_info_t peerInfo;

//Pin NEMA17
int STEP_PIN = 4;
int DIRECTION_PIN = 0;
bool change_rotation = true;

//Servo
#define SERVO_WRITE(n)     servo.write(n)
const int servo_pin = 2;
Servo servo;

//Display
#if USE_DISPLAY == 1
  #include <Arduino_GFX_Library.h>
  #include <U8g2lib.h>
  Arduino_DataBus *bus = new Arduino_HWSPI(17 /* DC */, 5 /* CS */);
  //Arduino_GFX *gfx = new Arduino_ST7789(bus, -1 /* RST */, 3 /* rotation */);
  Arduino_GFX *gfx = new Arduino_ST7789(bus, 14 /* RST */, 3 /* rotation */);
#endif

// Fonts
#if USE_DISPLAY == 1
  #include "./Fonts/Punk_Mono_Bold_120_075.h"           //10 x 7
  #include "./Fonts/Punk_Mono_Bold_160_100.h"           //13 x 9
  #include "./Fonts/Punk_Mono_Bold_200_125.h"           //16 x 12
  #include "./Fonts/Punk_Mono_Bold_240_150.h"           //19 x 14
  #include "./Fonts/Punk_Mono_Bold_320_200.h"           //25 x 18
  #include "./Fonts/Punk_Mono_Bold_600_375.h"           //48 x 36
  #include "./Fonts/Punk_Mono_Thin_120_075.h"           //10 x 7
  #include "./Fonts/Punk_Mono_Thin_160_100.h"           //13 x 9
  #include "./Fonts/Punk_Mono_Thin_240_150.h"           //19 x 14
#endif

//Logos
#if USE_DISPLAY == 1
  #include "./Resources/LogoTFT.h"
#endif

//Colors TFT
#if USE_DISPLAY == 1
  unsigned long  BACKGROUND = 0x0000;
  unsigned long  TEXT = 0xFFFF;
#endif

//OTA
int channel = 1;  //default channel if ESPNOW don't connect with a acces point
#if OTA_UPDATE == 1
  #include "./Resources/wifi.h"
  #include <WiFi.h>
  #include <WiFiClient.h>
  #include <WebServer.h>
  #include <ElegantOTA.h>                 /* aus dem Bibliotheksverwalter */
  WebServer server(80);
  unsigned long ota_progress_millis = 0;
  char ausgabe[30];
  bool ota_done = false;
#endif

//Pin Positionsswitch
#if SWITCH_TYPE == 0
  int SWITCH = 16;
#else
  int SWITCH = 22;
#endif

bool stepper_init_done = false;           //has to be true that the turntable works
bool move_jar_done = false;               //Flag to check move jar is done
bool move_pos_done = false;               //Flag to check move pos is done
bool move2pos_running = false;            //Flag if we are in the menu Move Jar
bool move_tp_done = false;                //Flaf if we are in the menu Tropprotection for the angle setting
bool drop_protection = false;             //fase --> drop protction open, true --> drop protection close
bool turntable_init_check = true;         //false --> turntable init check: off, true --> turntable init check on
int step_counter = 0;                     //counter for steps
int step_counter_value = 0;               //steps between two jars
int step_speed = 500;                     //Stepper speed (less is faster)
int step_speed_init = 500;                //Stepper speed to find the right position
int step_speed_run = 500;                 //Stepper speed in the run modus
int step_center_jar = 0;                  //Steps to center the jar on the scale 
int servo_min = 0;                        //min servo angle
int servo_max = 180;                      //max servo angle
int servo_speed = 0;                      //servo speed (lower is faster)
int servo_wait = 0;                       //waittime to open the dropprodection

int counter1 = 0;                         //Temp counter 1
int counter2 = 0;                         //Temp counter 2
int counter3 = 0;                         //Temp counter 3

//Variables
bool stop = false;
bool esp_now_init_success = false;
bool esp_now_msg_recived = false;
bool esp_now_send_error = true;
//bool esp_now_message_processed = false;
char esp_now_msg[] = "";
bool ota_update = false;

//ESP NOW
typedef struct messageToBeSent {
    char text[64];
    int value;
} messageToBeSent;

typedef struct receivedMessage {
    char text[64];
    int value;
} receivedMessage;

messageToBeSent myMessageToBeSent; 
receivedMessage myReceivedMessage;

int get_lenght(int i) {
  #if USE_DISPLAY == 1
    int res;
    if (i == -999 or i == -499) {res = 4;}
    else if (i < 10) {res = 1;}
    else if (i < 100) {res = 2;}
    else if (i < 1000) {res = 3;}
    else if (i < 10000) {res = 4;}
    else if (i < 100000) {res = 5;}
    return res;
  #else
    return 0;  //nur damit der compiler keine Warnung ausspuckt beil Kompilieren
  #endif
}

#if USE_DISPLAY == 1
  char myReceivedMessageTextOld[64];
  int myReceivedMessageValueOld = -999;
  char myMessageToBeSentTextOld[64];
  int myMessageToBeSentValueOld = -999;
  int stepper_init_done_old = -999;
  int step_speed_init_old = -999; 
  int step_speed_run_old = -999;
  int step_center_jar_old = -999;
  int drop_protection_old = -999;
  int servo_min_old = -999; 
  int servo_max_old = -999;
  int servo_speed_old = -999; 
  int servo_wait_old = -999;
  char revived_text_old[64] = "";
  int recived_value_old = -999;
  char text_display_check_recived[64];
  char text_display_check_send[64];
#endif

void update_display() {
  #if USE_DISPLAY == 1
    //recive mesage
    if(strcmp(myReceivedMessage.text, myReceivedMessageTextOld) != 0) {
      gfx->setTextBound(82, 108, 320 - 80, 21);
      gfx->fillRect(82, 86, 320 - 80, 22, BACKGROUND);
      gfx->fillRect(82, 108, 320 - 80, 21, BACKGROUND);
      gfx->setTextColor(RED);
      gfx->setCursor(85, 125);
      gfx->print(myReceivedMessage.text);
      gfx->print(" - ");
      gfx->print(myReceivedMessage.value);
      sprintf(myReceivedMessageTextOld, "%s", myReceivedMessage.text);
      myReceivedMessageValueOld = myReceivedMessage.value;
      sprintf(text_display_check_recived, "%s - %i", myReceivedMessage.text, myReceivedMessage.value);
      gfx->setTextBound(0, 0, 320, 240);
    }
    //send mesage
    if(strcmp(myMessageToBeSent.text, myMessageToBeSentTextOld) != 0) {
      gfx->fillRect(82, 86, 320 - 80, 21, BACKGROUND);
      gfx->fillRect(82, 108, 320 - 80, 21, BACKGROUND);
      gfx->setTextColor(RED);
      gfx->setCursor(85, 105);
      gfx->print(myMessageToBeSent.text);
      gfx->print(" - ");
      gfx->print(myMessageToBeSent.value);
      sprintf(myMessageToBeSentTextOld, "%s", myMessageToBeSent.text);
      myMessageToBeSentValueOld = myMessageToBeSent.value;
      sprintf(text_display_check_send, "%s - %i", myMessageToBeSent.text, myMessageToBeSent.value);
    }
  #endif
}

void update_display_check () {
  #if USE_DISPLAY == 1
    gfx->setTextBound(82, 108, 320 - 80, 21);
    if (strcmp(myReceivedMessage.text, "") == 0) {
      gfx->setTextColor(GREEN);
      gfx->setCursor(85, 125);
      gfx->print(text_display_check_recived);
      sprintf(myReceivedMessageTextOld, "%s", myReceivedMessage.text);
    }
    if (strcmp(myMessageToBeSent.text, "") == 0) {
      gfx->setTextColor(GREEN);
      gfx->setCursor(85, 105);
      gfx->print(text_display_check_send);
      sprintf(myMessageToBeSentTextOld, "%s", myMessageToBeSent.text);
    }
    gfx->setTextBound(0, 0, 320, 240);
  #endif
}

void update_display_init() {
  #if USE_DISPLAY == 1
    if (stepper_init_done != stepper_init_done_old) {
      gfx->setFont(Punk_Mono_Bold_160_100);
      int i = get_lenght(stepper_init_done_old);
      gfx->setCursor(145 - 9 * i, 150);
      gfx->setTextColor(BACKGROUND);
      gfx->print(stepper_init_done_old);
      i = get_lenght(stepper_init_done);
      gfx->setCursor(145 - 9 * i, 150);
      if (turntable_init_check == false) {gfx->setTextColor(BLUE);}
      else if (stepper_init_done == 1) {gfx->setTextColor(GREEN);}
      else {gfx->setTextColor(RED);}
      gfx->print(stepper_init_done);
      stepper_init_done_old = stepper_init_done;
    }
  #endif
}

void update_display_speed_init() {
  #if USE_DISPLAY == 1
    if (step_speed_init != step_speed_init_old) {
      gfx->setFont(Punk_Mono_Bold_160_100);
      int i = get_lenght(step_speed_init_old);
      gfx->setCursor(145 - 9 * i, 170);
      gfx->setTextColor(BACKGROUND);
      gfx->print(step_speed_init_old);
      i = get_lenght(step_speed_init);
      gfx->setTextColor(TEXT);
      gfx->setCursor(145 - 9 * i, 170);
      gfx->print(step_speed_init);
      step_speed_init_old = step_speed_init;
    }
  #endif
}

void update_display_speed_run() {
  #if USE_DISPLAY == 1
    if (step_speed_run != step_speed_run_old) {
      gfx->setFont(Punk_Mono_Bold_160_100);
      int i = get_lenght(step_speed_run_old);
      gfx->setCursor(315 - 9 * i, 170);
      gfx->setTextColor(BACKGROUND);
      gfx->print(step_speed_run_old);
      i = get_lenght(step_speed_run);
      gfx->setTextColor(TEXT);
      gfx->setCursor(315 - 9 * i, 170);
      gfx->print(step_speed_run);
      step_speed_run_old = step_speed_run;
    }
  #endif
}

void update_display_scenter_jar() {
  #if USE_DISPLAY == 1
    if (step_center_jar != step_center_jar_old) {
      gfx->setFont(Punk_Mono_Bold_160_100);
      int i = get_lenght(step_center_jar_old / 2);
      gfx->setCursor(315 - 9 * i, 150);
      gfx->setTextColor(BACKGROUND);
      gfx->print(step_center_jar_old / 2);
      i = get_lenght(step_center_jar / 2);
      gfx->setTextColor(TEXT);
      gfx->setCursor(315 - 9 * i, 150);
      gfx->print(step_center_jar / 2);
      step_center_jar_old = step_center_jar;
    }
  #endif
}

void update_display_dp_status() {
  #if USE_DISPLAY == 1
    if (drop_protection != drop_protection_old) {
      gfx->setFont(Punk_Mono_Bold_160_100);
      gfx->setTextColor(BACKGROUND);
      if (drop_protection_old == true) {
        gfx->setCursor(145 - 9 * 5, 195);
        gfx->print("close");
      }
      else {
        gfx->setCursor(145 - 9 * 4, 195);
        gfx->print("open");
      }
      gfx->setTextColor(TEXT);
      if (drop_protection == true) {
        gfx->setCursor(145 - 9 * 5, 195);
        gfx->print("close");
      }
      else {
        gfx->setCursor(145 - 9 * 4, 195);
        gfx->print("open");
      }
      drop_protection_old = drop_protection;
    }
  #endif
}

void update_display_dp_speed() {
  #if USE_DISPLAY == 1
    if (servo_speed != servo_speed_old) {
      gfx->setFont(Punk_Mono_Bold_160_100);
      int i = get_lenght(servo_speed_old);
      gfx->setCursor(315 - 9 * i, 195);
      gfx->setTextColor(BACKGROUND);
      gfx->print(servo_speed_old);
      i = get_lenght(servo_speed);
      gfx->setTextColor(TEXT);
      gfx->setCursor(315 - 9 * i, 195);
      gfx->print(servo_speed);
      servo_speed_old = servo_speed;
    }
  #endif
}

void update_display_dp_angle_min() {
  #if USE_DISPLAY == 1
    if (servo_min != servo_min_old) {
      gfx->setFont(Punk_Mono_Bold_160_100);
      int i = get_lenght(servo_min_old);
      gfx->setCursor(145 - 9 * i, 215);
      gfx->setTextColor(BACKGROUND);
      gfx->print(servo_min_old);
      i = get_lenght(servo_min);
      gfx->setTextColor(TEXT);
      gfx->setCursor(145 - 9 * i, 215);
      gfx->print(servo_min);
      servo_min_old = servo_min;
    }
  #endif
}

void update_display_dp_angle_max() {
  #if USE_DISPLAY == 1
    if (servo_max != servo_max_old) {
      gfx->setFont(Punk_Mono_Bold_160_100);
      int i = get_lenght(servo_max_old);
      gfx->setCursor(315 - 9 * i, 215);
      gfx->setTextColor(BACKGROUND);
      gfx->print(servo_max_old);
      i = get_lenght(servo_max);
      gfx->setTextColor(TEXT);
      gfx->setCursor(315 - 9 * i, 215);
      gfx->print(servo_max);
      servo_max_old = servo_max;
    }
  #endif
}

void update_display_dp_close_wait_time() {
  #if USE_DISPLAY == 1
    if (servo_wait != servo_wait_old) {
      gfx->setFont(Punk_Mono_Bold_160_100);
      int i = get_lenght(servo_wait_old);
      gfx->setCursor(315 - 9 * i, 235);
      gfx->setTextColor(BACKGROUND);
      gfx->print(servo_wait_old);
      i = get_lenght(servo_wait);
      gfx->setTextColor(TEXT);
      gfx->setCursor(315 - 9 * i, 235);
      gfx->print(servo_wait);
      servo_wait_old = servo_wait;
    }
  #endif
}
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
void loop() {
  //Display
  update_display_init();
  update_display_speed_init();
  update_display_speed_run();
  update_display_scenter_jar();
  update_display_dp_status();
  update_display_dp_speed();
  update_display_dp_angle_min();
  update_display_dp_angle_max();
  update_display_dp_close_wait_time();
  while (esp_now_msg_recived == false) {
    if (stop == true) {
      delESPnowArrays();
      strcpy(myMessageToBeSent.text, "ok_stop");
      sendMessage();
      stop = false;
    }
    if (digitalRead(SWITCH) == 1 and stepper_init_done == true and strcmp(myReceivedMessage.text, "move_pos") != 0 and turntable_init_check == true and stop == false) {  //Stepper init zurücksetzen, fals einer der Drehteller von Hand verschiebt
      delay(500);
      if (digitalRead(SWITCH) == 1) {
        stepper_init_done = false;
      }
      break;
    }
    delay(10);
  }
  if (esp_now_msg_recived == true) {
    if (strcmp(myReceivedMessage.text, "move_pos") != 0) {
      move2pos_running = false;
    }
    if (strcmp(myReceivedMessage.text, "check") == 0) {
      update_display();
      delESPnowArrays();
      if (stepper_init_done == true) {strcpy(myMessageToBeSent.text, "ok_init");}
      else                           {strcpy(myMessageToBeSent.text, "nok_init");}
      sendMessage();
      #ifdef DEBUG
        Serial.print("myMessageToBeSent: "); Serial.println(myMessageToBeSent.text);
      #endif
    }
    else if (strcmp(myReceivedMessage.text, "speed_init") == 0) {
      update_display();
      delESPnowArrays();
      strcpy(myMessageToBeSent.text, "ok_speed_init");
      myMessageToBeSent.value = step_speed_init;
      sendMessage();
    }
    else if (strcmp(myReceivedMessage.text, "speed_run") == 0) {
      update_display();
      delESPnowArrays();
      strcpy(myMessageToBeSent.text, "ok_speed_run");
      myMessageToBeSent.value = step_speed_run;
      sendMessage();
    }
    else if (strcmp(myReceivedMessage.text, "ts_angle_min") == 0) {
      update_display();
      delESPnowArrays();
      strcpy(myMessageToBeSent.text, "ok_ts_angle_min");
      myMessageToBeSent.value = servo_min;
      sendMessage();
    }
    else if (strcmp(myReceivedMessage.text, "ts_angle_max") == 0) {
      update_display();
      delESPnowArrays();
      strcpy(myMessageToBeSent.text, "ok_ts_angle_max");
      myMessageToBeSent.value = servo_max;
      sendMessage();
    }
    else if (strcmp(myReceivedMessage.text, "ts_waittime") == 0) {
      update_display();
      delESPnowArrays();
      strcpy(myMessageToBeSent.text, "ok_ts_waittime");
      myMessageToBeSent.value = servo_wait;
      sendMessage();
    }
    else if (strcmp(myReceivedMessage.text, "ts_speed") == 0) {
      update_display();
      delESPnowArrays();
      strcpy(myMessageToBeSent.text, "ok_ts_speed");
      myMessageToBeSent.value = servo_speed;
      sendMessage();
    }
    else if (strcmp(myReceivedMessage.text, "speed_init_save") == 0) {
      update_display();
      preferences.putUInt("step_speed_init", myReceivedMessage.value);
      readPreferences();
      delESPnowArrays();
      strcpy(myMessageToBeSent.text, "ok_speed_init_save");
      myMessageToBeSent.value = step_speed_init;
      sendMessage();
    }
    else if (strcmp(myReceivedMessage.text, "speed_run_save") == 0) {
      update_display();
      preferences.putUInt("step_speed_run", myReceivedMessage.value);
      readPreferences();
      delESPnowArrays();
      strcpy(myMessageToBeSent.text, "ok_speed_run_save");
      myMessageToBeSent.value = step_speed_run;
      sendMessage();
    }
    else if (strcmp(myReceivedMessage.text, "pos_jar_steps_save") == 0) {
      update_display();
      preferences.putUInt("step_center_jar", myReceivedMessage.value);
      readPreferences();
      delESPnowArrays();
      strcpy(myMessageToBeSent.text, "ok_pos_jar_steps_save");
      myMessageToBeSent.value = step_center_jar;
      sendMessage();
    }
    else if (strcmp(myReceivedMessage.text, "ts_angle_min_save") == 0) {
      update_display();
      preferences.putUInt("servo_min", myReceivedMessage.value);
      readPreferences();
      delESPnowArrays();
      strcpy(myMessageToBeSent.text, "ok_ts_angle_min_save");
      myMessageToBeSent.value = servo_min;
      sendMessage();
    }
    else if (strcmp(myReceivedMessage.text, "ts_angle_max_save") == 0) {
      update_display();
      preferences.putUInt("servo_max", myReceivedMessage.value);
      readPreferences();
      delESPnowArrays();
      strcpy(myMessageToBeSent.text, "ok_ts_angle_max_save");
      myMessageToBeSent.value = servo_max;
      sendMessage();
    }
    else if (strcmp(myReceivedMessage.text, "ts_waittime_save") == 0) {
      update_display();
      preferences.putUInt("servo_wait", myReceivedMessage.value);
      readPreferences();
      delESPnowArrays();
      strcpy(myMessageToBeSent.text, "ok_ts_waittime_save");
      myMessageToBeSent.value = servo_wait;
      sendMessage();
    }
    else if (strcmp(myReceivedMessage.text, "ts_speed_save") == 0) {
      update_display();
      preferences.putUInt("servo_speed", myReceivedMessage.value);
      readPreferences();
      delESPnowArrays();
      strcpy(myMessageToBeSent.text, "ok_ts_speed_save");
      myMessageToBeSent.value = servo_speed;
      sendMessage();
    }
    else if (strcmp(myReceivedMessage.text, "init") == 0) {
      update_display();
      delESPnowArrays();
      stepper_init();
      if (stepper_init_done == true) {strcpy(myMessageToBeSent.text, "ok_init_done");}
      else                           {strcpy(myMessageToBeSent.text, "nok_init_done");}
      sendMessage();
    }
    else if (strcmp(myReceivedMessage.text, "move_jar") == 0 and stepper_init_done == true) {
      update_display();
      delESPnowArrays();
      move_jar();
      if (move_jar_done == true) {strcpy(myMessageToBeSent.text, "ok_move_jar");}
      else                       {strcpy(myMessageToBeSent.text, "nok_move_jar");}
      move_jar_done = false;
      sendMessage();
    }
    else if (strcmp(myReceivedMessage.text, "move_pos") == 0) {
      update_display();
      if (move2pos_running == false) {
        stepper_init_done = false;
      }
      move2pos_running = true;
      move_pos();
      delESPnowArrays();
      if (move_pos_done == true) {strcpy(myMessageToBeSent.text, "ok_move_pos");}
      else                       {strcpy(myMessageToBeSent.text, "nok_move_pos");}
      move_pos_done = false;
      sendMessage();
    }
    else if (strcmp(myReceivedMessage.text, "move_dp") == 0) {
      int i = myReceivedMessage.value;
      update_display();
      delESPnowArrays();
      move_tp(i);
      if (move_tp_done == true) {strcpy(myMessageToBeSent.text, "ok_move_tp");}
      else                       {strcpy(myMessageToBeSent.text, "nok_move_tp");}
      move_tp_done = false;
      sendMessage();
    }
    else if (strcmp(myReceivedMessage.text, "close_drop_prodection") == 0) {
      update_display();
      delESPnowArrays();
      close_drop_protection(0);
      if (drop_protection == true) {strcpy(myMessageToBeSent.text, "ok_close_dp");}
      else                         {strcpy(myMessageToBeSent.text, "nok_close_dp");}
      sendMessage();
    }
    else if (strcmp(myReceivedMessage.text, "open_drop_prodection") == 0) {
      update_display();
      delESPnowArrays();
      open_drop_protection();
      if (drop_protection == false) {strcpy(myMessageToBeSent.text, "ok_open_dp");}
      else                          {strcpy(myMessageToBeSent.text, "nok_open_dp");}
      sendMessage();
    }
    else if (strcmp(myReceivedMessage.text, "turn_on_stepper_init_check") == 0) {
      update_display();
      delESPnowArrays();
      turntable_init_check = true;
      strcpy(myMessageToBeSent.text, "ok_on_init_check");
      sendMessage();
    }
    else if (strcmp(myReceivedMessage.text, "turn_off_stepper_init_check") == 0) {
      update_display();
      delESPnowArrays();
      turntable_init_check = false;
      strcpy(myMessageToBeSent.text, "ok_off_init_check");
      sendMessage();
    }
    else if (strcmp(myReceivedMessage.text, "ota_update_status") == 0) {
      update_display();
      delESPnowArrays();
      strcpy(myMessageToBeSent.text, "ok_ota_update_status");
      myMessageToBeSent.value = ota_update;
      sendMessage();
    }
    #if OTA_UPDATE == 1
      else if (strcmp(myReceivedMessage.text, "enable_ota_update") == 0) {
        update_display();
        delESPnowArrays();
        OTASetup();
        ota_done = false;
      }
      else if (strcmp(myReceivedMessage.text, "stop_ota_update") == 0) {
        update_display();
        delESPnowArrays();
        strcpy(myMessageToBeSent.text, "ok_stop_ota_update");
        sendMessage();
        ota_done = false;
      }
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
